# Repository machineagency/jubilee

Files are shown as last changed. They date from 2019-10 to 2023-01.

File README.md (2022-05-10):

Jubilee V2.2.2
=======

Jubilee is an open-source, extensible multi-tool motion platform capable of running GCode for non-loadbearing automation applications.

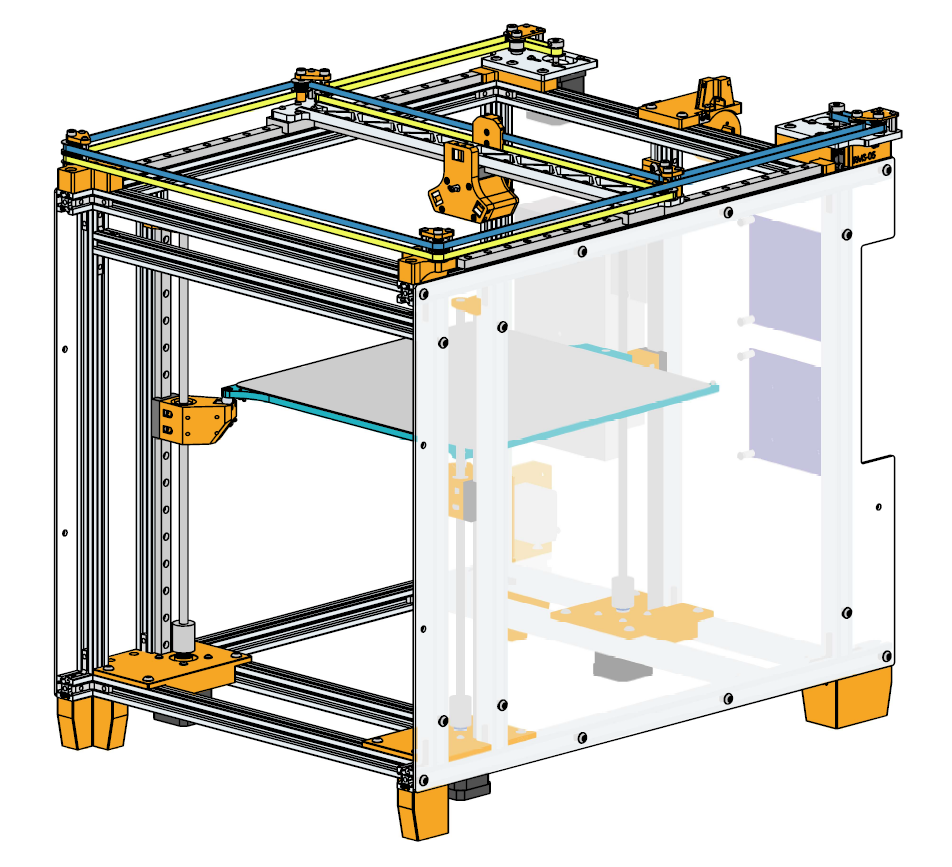
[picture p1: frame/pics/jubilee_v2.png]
Jubilee


Out-of-the-box, Jubilee is configured for multimaterial 3D printing and multicolor pen plotting, but we've had success with light liquid-handling and image stitching applications too.

While this repository contains all the design-related content needed to build a Jubilee, we suggest using the [**Wiki**](https://jubilee3d.com/index.php?title=Main_Page) to navigate through this "file soup."

## Top-Level Specs
* Automatic Toolchanging compatible with E3D tool plates
* CoreXY Motion System
* 300x300x300 build volume.
* 409mm of horizontal tool rack space
* kinematically coupled bed plate
* autotramming with 3-point bed-leveling
* ~$1350 for a single unit, not including tools. See the [BOM][bom] for the part breakdown
* User Extensible! We encourage extending the design to custom applications via custom tools and bed plates
* Full specs listed on [this wiki page](https://jubilee3d.com/index.php?title=Specs)

## Build your own Jubilee

The best way to get started is to thumb through the [**Assembly Instructions**](https://jubilee3d.com/index.php?title=Assembly_Instructions) and [**Bill of Materials**][bom] first.

Then head over to the [**Wiki**](https://jubilee3d.com/index.php?title=Main_Page) to start gathering tools and deciding which parts to buy and which parts to make.

### Downloading
There are 3 ways to work with the Jubilee source files: with and without history.
* To download the latest stable release without history, head to the [Releases](https://github.com/machineagency/jubilee/releases) page and download the latest release.
* To download the latest stable release with history and track updates, clone the project with the "Code" button above and switch to the corresponding branch.
* To download the latest stable release with history and submit additions back to the main project, create a "Fork" of the project with the button in the upper right. Then switch to the corresponding release branch in your fork of the project.

## Repository Contents
The Repository is broken into three main chunks:
* **frame** contains all design content related to the Jubilee frame
* **tools** contains all design content related to custom tools and tools to help assemble and tune Jubilee
* **software** holds both the Duet config files and profile settings for common slicer packages

inside these folders, you'll usually find a folder structure that looks like this:
* **assembly\_instructions** contains PDFs to take you step-by-step through sub-assemblies of the project.
* **cads** contains raw design files in two formats
    * **Solidworks**
    * **STEP**
* **fabrication\_exports** contains STLs, DXFs, and other files used to fabricate pieces of Jubilee

## Support

Have questions? Building your own Jubilee? **[Join the Discord!][discord]**

## Contributing

Jubilee is meant to be extended by the community. If you are interested in contributing, there are a number of ways to get involved:

* Review, comment, or add to the **[open issues](https://github.com/machineagency/jubilee/issues)**
* Have a new tool to add to the repository? Read our [contributing]() guidlelines and create a [pull request](https://help.github.com/en/github/collaborating-with-issues-and-pull-requests/creating-a-pull-request)
* **[Join the Discord!][discord]**

## Who are we?
Jubilee was designed with love by [Joshua Vasquez](http://www.doublejumpelectric.com/) of [Machine Agency](http://depts.washington.edu/machines/) at the University of Washington.

### Press and Outside Resources

Read more about the history of Jubilee on [Hackaday](https://hackaday.com/2019/11/14/jubilee-a-toolchanging-homage-to-3d-printer-hackers-everywhere/), or, for the patient, check out this (1hr) [talk](https://www.youtube.com/watch?v=7fz2UHHxe5o&t=119s) given in Jan 2020.
For more community takes, have a look at:
* [Hackster.io](https://www.hackster.io/news/jubilee-is-an-open-source-motion-platform-that-allows-for-multi-tool-fabrication-213881ee3ce1)
* 3D Distributed
    * [Best CoreXY 3D Printers 2020](https://3ddistributed.com/best-corexy-3d-printer-2020/)
    * [Best CoreXY 3D Printers 2021](https://3ddistributed.com/corexy-3d-printer/best-corexy-3d-printers-2021/)
* [All3DP](https://all3dp.com/2/3d-printer-plans-3d-printer-blueprints/)
* [3D Printing Today](https://threedprintingtoday.libsyn.com/327_3dprinting_today)

### Open Source
Jubilee is licensed under a [Creative Commons Attribution 4.0 Unported License][cc-by] (CC BY 4.0).
and [Certified Open Source Hardware](https://certification.oshwa.org/us002091.html).

[][cc-by] 

[bom]: https://docs.google.com/spreadsheets/d/1pRzBQxVzL9c4T9b1RrKvSjlSwJJhJ7NcbSV6iJUv0X0/edit#gid=0
[cc-by]: https://creativecommons.org/licenses/by/4.0/
[cc-by-image]: https://licensebuttons.net/l/by/4.0/88x31.png
[discord]: https://discord.gg/XkphRqb
[wiki]: https://jubilee3d.com/

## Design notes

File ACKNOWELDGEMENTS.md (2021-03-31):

Jubilee was built to encapsulate all the best practices in hobbyist 3D printing machine design at the time.
As a result, it's a machine that takes inspiration from many many places.
Here's the (growing!) list of referenced projects and contributors

## Design Acknowledgments
* Nadya Peek of Machine Agency
  * for the time, expenses, and infrastructure that enabled Jubilee to come together over many iterations
* Eric Moyer
  * for continuous design feedback, manufacturing insights, and help with community engagement
* Sanjay Mortimer and the E3D Team
  * for an open reference for tool coupling
* J Steve White and Tony Akens of the [Railcore](https://railcore.org/) Project
  * for an incredibly well-documented BOM, an example of 3-point bed leveling firmware configs, a great example of community engagement, and openness in sharing and answering questions
* @marioquake on Github for suggesting a well-placed spacer
* @Ocho Camino on Discord for an improved Power Inlet Socket
* @Troll on Discord for a fantastic Logo on the bed plate rendering
* @edthesped for the "Cappuccino"-tested Fan Shroud

## Manufacturing and Supplier Acknowledgements
* Matthew White at 713Maker
  * for supporting the Jubilee builder community with custom machined parts and developing the original magnetic bed plate
* Steve Wygant of SeeMeCNC
  * for supporting the Jubilee builder community with a generous variety of Jubilee's laser-cut and machined parts.
* Wade Wendorf at Mandala Rose Works
  * for supporting the Jubilee builder community with custom machined upgrade parts of various types
* Luke at Luke's Laboratory
  * for kit-izing various elements of the project, making them cheaper for Jubilee builders
* Rebecca and Jason of LDO Motors
  * for supplying custom motor options for the toolchanger elastic lock design

## Grants and Donations
Jubilee is made possible through monetary support and donations from
* the 2019 [Tool Foundry](https://www.toolfoundry.org/) Boot Camp Accelerator
* The E3D Team
* Tony Lock of the Duet3D Project

## Beta Testing and Design Feedback Acknowledgements
* Andrew Waer for an early V1 build with assembly feedback and research into trade-offs regarding various documentation styles
* Cindy Feng for an early V2 build with extensive feedback
* Kellie Dunn for an early V2 build with extensive feedback
* @Danal on Discord for early design feedback and identifying early stage bugs

## BOM and Documentation Acknoweldgements
* @ImpC on Discord for BOM alternatives to cut costs
* @VinnyCordeiro on Discord for contributing a massive list of laser cutting services to the wiki
* @MiasmicTruth on Discord for live assembly videos and continuous assembly instruction feedback
* @Bryan H. on Discord for part numbering scheme suggestions and printed part fabrication suggestions
* @Enza3D on Discord for part numbering scheme suggestions
* @RexOrient on Discord for Duet3 Wiring Diagrams

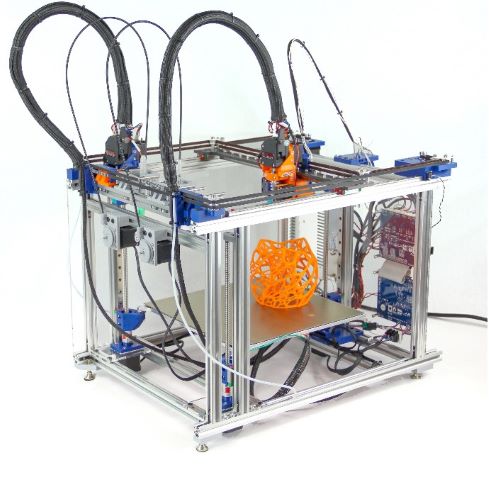
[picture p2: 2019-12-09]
frame/pics/jubilee-professional-headshot-brightened.jpg

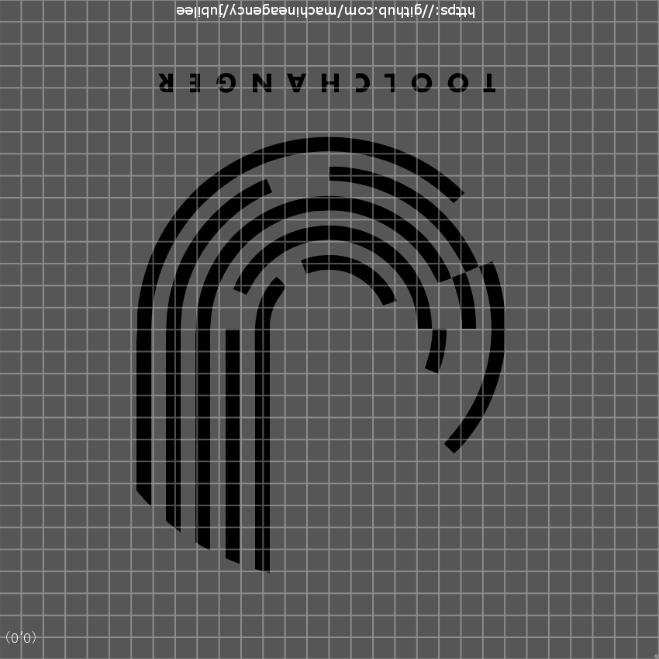
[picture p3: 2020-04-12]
software/slicer_settings/prusa_slic3r/bed_rendering/Jubilee_Bed_Graphic.png

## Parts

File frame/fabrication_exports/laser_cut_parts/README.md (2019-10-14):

## Notes on File Types

Most laser cutters will directly trace the lines and arcs present in a DXF file. For these laser cutters, use the **offset** files.

For the few laser cutters that perform *kerf compensation*, use the **original** files.

If you are unsure, using the **offset** files is probably your best bet.

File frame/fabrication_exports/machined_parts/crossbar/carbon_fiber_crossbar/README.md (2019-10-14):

## Getting a Crossbar

To have this part made for you, send this DXF to cncmadness@gmail.com. Request that this part be made out of **6mm carbon fiber plain-weave**. The estimated price for this part is between $50 and $60.

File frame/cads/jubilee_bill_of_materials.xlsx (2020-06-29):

ITEM NO. | QTY. | DESCRIPTION | Part Num | Part Num Short | Stock Material | Fab Process | Vendor | Vendor Num
1 | 1 | Twist Lock Shaft |  |  | Stainless Steel | Machined
2 | 7 | 409mm TSlot Extrusion |  |  |  |  | Misumi | HFS5-2020-409
3 | 4 | 604mm long TSlot Extrusion |  |  |  |  | Misumi | HFS5-2020-604
4 | 7 | 430mm 2020 TSlot Extrusion |  |  |  |  | Misumi | HFS5-2020-430
5 | 4 | MGN12C Carriage Block |  |  |  |  | Aliexpress | n/a
6 | 2 | MGN12H Carriage Block |  |  |  |  | Aliexpress | n/a
7 | 3 | length@mgn12_rail_400mm.SLDPRTmm long MGN12 rail |  |  |  |  | Aliexpress
8 | 1 | length@mgn12_rail_395mm.SLDPRTmm long MGN12 rail |  |  |  |  | Aliexpress | n/a
9 | 2 | 450"mm long $PRP:"SW-Configuration Name |  |  |  |  | Aliexpress
10 | 6 | 20T Idler pulley, 2GT, 5mm bore |  |  |  |  | Amazon | B07GLQMMLJ
11 | 2 | 20T toothless idler, 5mm bore |  |  |  |  | Amazon | B071KK6Z8X
12 | 1 | Duet Ethernet Expansion Board |  |  |  |  | Duet3d
13 | 1 | Duet Ethernet |  |  |  |  | Duet3d
14 | 3 | 8mm T8x2 Trapezoidal Lead Screw |  |  |  |  | ZYLTech | HW-SC-T8x2-Delrin-CUTSMALL
15 | 3 | 5mm to 8mm flexible plumb coupler |  |  |  |  | ZYLtech | HW-CP-PUM-5x8
16 | 3 | 8mm T8x2 Small Delrin Anti-Backlash Nut |  |  |  |  | ZYLTech | n/a
17 | 2 | 16-T 2GT Drive Pulley for 6mm belt |  |  |  |  | E3D-Online | M-PULLEY-GT2-16T-6-P5-C-H155
18 | 2 | 20T Idler pulley, 2GT, 5mm bore |  |  |  |  | Amazon | B07GLQMMLJ
19 | 2 | 20T Toothless Idler pulley, 2GT, 5mm bore
20 | 1 | Upper Belt
21 | 1 | Lower Belt
22 | 1 | Hub, 6mm bore |  |  |  |  | Filastruder
23 | 27 | M3 Slide In T Nuts
24 | 3 | 10mm steel balls with M4 threads |  |  |  |  | Newegg | DZ6YTSFkoC
25 | 1 | Bed Plate |  |  | 6.35mm MIC6 Aluminum | Machined | 713Maker
26 | 1 | Pocketed Crossbar |  |  | 6mm carbon fiber plain weave |  | Mandala Rose Works
27 | 1 | Machined Left Motor Corner Bracket | 021-LMP-02-M61 | LMP-02 | 6061 | Machined | Mandala Rose Works
28 | 1 | Machined Right Motor Corner Bracket | 021-RMP-02-M61 | RMP-02 | 6061 | Machined | Mandala Rose Works
29 | 1 | M3 Square Nut |  |  |  |  | Misumi | HNSQ3-3
30 | 1 | 24V Power Supply |  |  |  |  | Amazon | B01IOK5FM0
31 | 1 | IEC320 C14 120V Power Socket |  |  |  |  | Amazon | B07C184P7L
32 | 56 | Interior Inside Corner Bracket |  |  |  |  | Amazon | B07F2K8SN7
33 | 89 | M5 Drop-In T-Nut for 20x20 Extrusion |  |  |  |  | Amazon | B01FOC6A8E
34 | 4 | OpenBuilds M5 3mm Spacer
35 | 5 | Nema 17 Stepper Motor |  |  |  |  | Stepper Online | 17HM19-2004S or 17HM19-2004S1
36 | 1 | Nema 11 Planetary Stepper,13.76:1, 1A |  |  |  |  | Stepper Online | 14HS13-0804S-PG5
37 | 16 | M5 Shim, 0.2mm thick, 7mm OD |  |  |  |  | Misumi | CIMRS5-7-0.2
38 | 1 | M3 Set Screw, 5mm long |  |  |  |  | McMaster-Carr | 92029A102
39 | 3 | M2 Screw, 10mm long |  |  |  |  | McMaster-Carr | 91292A833
40 | 19 | M3 Buttonhead Screw, 6mm long |  |  |  |  | McMaster-Carr | 92095A179
41 | 72 | M3 Buttonhead Screw, 8mm long |  |  |  |  | McMaster-Carr | 92095A181
42 | 53 | M3 Buttonhead Screw, 10mm long |  |  |  |  | McMaster-Carr | 92095A182
43 | 12 | M3 Buttonhead Screw, 12mm long |  |  |  |  | McMaster-Carr | 92095A183
44 | 1 | M3 Buttonhead Screw, 16mm long |  |  |  |  | McMaster-Carr | 92095A184
45 | 1 | M3 Buttonhead Screw, 20mm long |  |  |  |  | McMaster-Carr | 92095A185
46 | 4 | M4 Buttonhead Screw, 6mm long |  |  |  |  | McMaster-Carr | 92095A188
47 | 16 | M4 Buttonhead Screw, 8mm long |  |  |  |  | McMaster-Carr | 92095A189
48 | 2 | M4 Buttonhead Screw, 10mm long |  |  |  |  | McMaster-Carr | 92095A190
49 | 46 | M5 Buttonhead Screw, 8mm long |  |  |  |  | McMaster-Carr | 92095A207
50 | 27 | M5 Buttonhead Screw, 10mm long |  |  |  |  | McMaster-Carr | 92095A208
51 | 10 | M5 Buttonhead Screw, 20mm long |  |  |  |  | McMaster-Carr | 92095A214
52 | 4 | M5 Buttonhead Screw, 30mm long |  |  |  |  | McMaster-Carr | 92095A218
53 | 2 | M3 Flathead Screw, 10mm long |  |  |  |  | McMaster-Carr | 92125A130
54 | 3 | M4 Flathead screw, 10mm long |  |  |  |  | McMaster-Carr | 92125A190
55 | 1 | M3 Set Screw, 3mm long |  |  |  |  | McMaster-Carr | 92015A101
56 | 1 | M3 Set Screw, 8mm long |  |  |  |  | McMaster-Carr | 91390A101
57 | 2 | M4 Set Screw, 25mm long |  |  |  |  | McMaster-Carr | 92605A124
58 | 16 | M3 Locknut |  |  |  |  | McMaster-Carr | 93625A100
59 | 2 | M4 Locking Nut |  |  |  |  | McMaster-Carr | 93625A150
60 | 22 | M3 Washer |  |  |  |  | McMaster-Carr | 90965A130
61 | 8 | M4 Nylon Washer |  |  |  |  | McMaster-Carr | 95610A150
62 | 1 | M3 Dowel Pin, 12mm long |  |  |  |  | McMaster-Carr | 91585A371
63 | 12 | M4 Dowel Pin, 20mm long |  |  |  |  | McMaster-Carr | 91585A457
64 | 4 | M4 Shoulder Screw, 16mm-l, 5mm-d |  |  |  |  | McMaster-Carr | 90265A132
65 | 6 | M4 Shoulder Screw, 25mm long |  |  |  |  | McMaster-Carr | 90278A375
66 | 1 | M3 10mm standoff, 4.5mm wide |  |  |  |  | McMaster-Carr | 95947A006
67 | 4 | M3 Standoff, 14mm long, 6mm wide |  |  |  |  | McMaster-Carr | 95947A045
68 | 5 | M3 Standoff, 20mm long, 6mm wide |  |  |  |  | McMaster-Carr | 95947A054
69 | 8 | M4 Standoff, 12mm long |  |  |  |  | McMaster-Carr | 95947A041
70 | 22 | M3 Tapered Heat Set Insert |  |  |  |  | McMaster-Carr | 94180A331
71 | 4 | M4 Tapered Long Heat Set Insert |  |  |  |  | McMaster-Carr | 94180A353
72 | 4 | M5 Washer, 0.8-1.2mm thick |  |  |  |  | McMaster-Carr | 98687A110
73 | 3 | M5 Shim, 0.2mm thick, 10mm OD |  |  |  |  | McMaster-Carr | 98089A246
74 | 1 | M6 Shim, 0.2mm thick |  |  |  |  | McMaster-Carr | 98089A247
75 | 1 | E-Clip |  |  |  |  | McMaster-Carr | 98543A103
76 | 1 | Sleeve Bearing, 6mm bore, 10mm long |  |  |  |  | McMaster-Carr | 6658K726
77 | 2 | M5 Buttonhead Screw, 14mm long |  |  |  |  | McMaster-Carr | 92095A211
78 | 3 | 5mm Oversize Thrust Bearing |  |  |  |  | McMaster-Carr | 6655K51
79 | 1 | Ring Lug Thermistor |  |  |  |  | Digikey | BC2891-ND
80 | 2 | Mechanical Limit Switch |  |  |  |  | Digikey | SS0750300F070P1A-ND
81 | 1 | 3-32V Solid State Relay |  |  |  |  | Digikey | CC1006-ND
82 | 3 | Dust-Proof Limit Switch |  |  |  |  | Digikey | SW1153-ND
83 | 3 | Bent Solder Terminal Lug |  |  |  |  | Digikey | 36-4000-ND
84 | 2 | Bent M3 Solder Terminal Lug (Bend A) |  |  |  |  | Digikey | 36-7328-ND
85 | 3 | Bent M3 Solder Terminal Lug (Bend A) |  |  |  |  | Digikey | 36-4000-ND
86 | 1 | Front Left Z Motor Plate | 10-LZP-03-PPL | LZP-03 | PLA | Printed
87 | 1 | Front Right Z Motor Plate | 10-LZP-03-PPL | LZP-03 | PLA | Printed
88 | 1 | Back Z Motor Plate | 10-BZP-03-PPL | BZP-03 | PLA | Printed
89 | 1 | Back Right Foot | 10-BRF-05-PPL | BRF-05 | PLA | Printed
90 | 1 | Back Left Foot | 10-BRF-05-PPL | BRF-05 | PLA | Printed
91 | 1 | Front Right Foot | 10-BRF-05-PPL | BRF-05 | PLA | Printed
92 | 1 | Front Left Foot | 10-BRF-05-PPL | BRF-05 | PLA | Printed
93 | 3 | Z Thrust Bearing Spacer |  |  | PLA | Printed
94 | 1 | Left Corner Pulley Plate | 03-LCP-02-PPL | LCP-02 | PLA | Printed
95 | 1 | Left Corner Pulley Plate | 03-RCP-02-PPL | RCP-02 | PLA | Printed
96 | 1 | Right Motor Spacer | 02-RMS-05-PPE | RMS-05 | PLA | Printed
97 | 1 | Lock Actuator Base Plate | 05-RLB-10-PPL | RLB-10 | PLA | Printed
98 | 1 | Left Motor Spacer | 02-LMS-04-PPE | LMS-04 | PLA | Printed
99 | 2 | Belt Clasp | 06-BCL-02-PPL | BCL-02 | PLA | Printed
100 | 1 | Carriage Center Plate | 06-CCP-04-PPL | CCP-04 | PLA | Printed
101 | 1 | Carriage Back Plate | 06-CCP-04-PPL | CCP-04 | PLA | Printed
102 | 1 | Carriage Front Plate | 06-CCP-04-PPL | CCP-04 | PLA | Printed
103 | 1 | Spring Guide Capture | 06-CCP-04-PPL | CCP-04 | PLA | Printed
104 | 1 | Carriage Pulley | 06-CPL-01-PPL | CPL-01 | PLA | Printed
105 | 1 | Back Leadscrew Retainer | 12-BLR-03-PPL | BLR-03 | PLA | Printed
106 | 1 | Front Left Leadscrew Retainer | 12-LLR-03-PPL | LLR-03 | PLA | Printed
107 | 1 | Front Right Leadscrew Retainer | 12-LLR-03-PPL | LLR-03 | PLA | Printed
108 | 3 | Printed Pulley Spacer |  |  | PLA | Printed
109 | 1 | Left Bed Coupler | 12-RBC-04-PPL | RBC-04 | PLA | Printed
110 | 1 | Right Bed Coupler | 12-RBC-04-PPL | RBC-04 | PLA | Printed
111 | 1 | Back Bed Coupler | 12-BBC-04-PPL | BBC-04 | PLA | Printed
112 | 2 | pulley reinforcement plate for motor | -MRP-01- | MRP-01 | PLA | Printed
113 | 1 | Left Crossbar Pulley Reinforcement Plate | 041-LXR-03-PPL | LXR-03 | PLA | Printed
114 | 1 | Right Crossbar Pulley Reinforcement Plate | 041-RXR-03-PPL | RXR-03 | PLA | Printed
115 | 1 | PSU Socket Holder | 09-PSH-02-PPL | PSH-02 | PLA | Printed
116 | 1 | Spring Guide Anchor Block | 05-RLB-10-PPL | RLB-10 | PLA | Printed
117 | 1 | Lock Actuator Motor Clip |  |  | PLA | Printed
118 | 1 | REL Knob |  |  | PLA | Printed
119 | 1 | Fixed Pulley |  |  | PLA | Printed
120 | 1 | Left Corner Pulley Reinforcement Plate | 03-LCR-03-PPL | LCR-03 | PLA | Printed
121 | 1 | Left Corner Pulley Reinforcement Plate | 03-LCR-03-PPL | LCR-03 | PLA | Printed
122 | 1 | Crossbar X Limit Trigger |  |  | PLA | Printed
123 | 1 | Floating Pulley |  |  | PLA | Printed
124 | 1 | Twist Lock Spacer |  |  | PLA | Printed
125 | 1 | Left Side Panel |  |  | 3mm Acrylic Sheet | Laser Cut
126 | 1 | Right Side Panel |  |  | 3mm Acrylic Sheet | Laser Cut
127 | 1 | Back Panel |  |  | 3mm Acrylic Sheet | Laser Cut
128 | 1 | Magnetic Sheet (305x305mm) |  |  |  |  | Subtle.Design

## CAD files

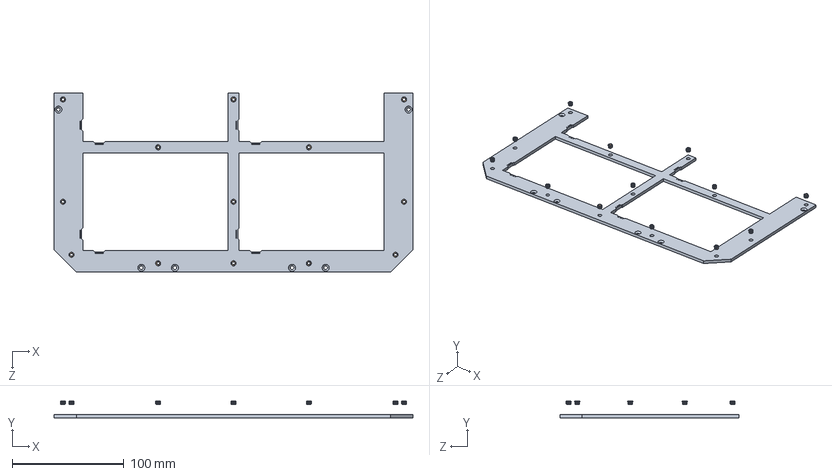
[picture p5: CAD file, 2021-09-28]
bed_plates/6x_well_plate_bed/cads/Solidworks/top_layer_bottom_plate_with_inserts.SLDASM
321.0 x 15.1 x 160.5 mm
segmented_6_slot_bed_attachment
m3_heat_set_insert_tokai_ud-43030 x 13

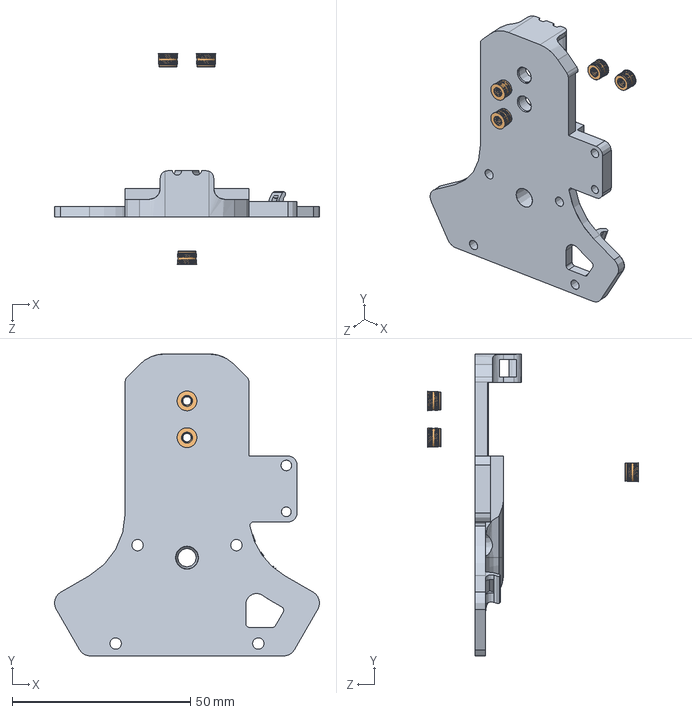
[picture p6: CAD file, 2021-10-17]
frame/cads/Solidworks/jubilee_frame/carriage/carriage_back_plate_with_inserts.SLDASM
74.3 x 84.7 x 59.2 mm
carriage
m3_heat_set_insert_94180A331 x 4

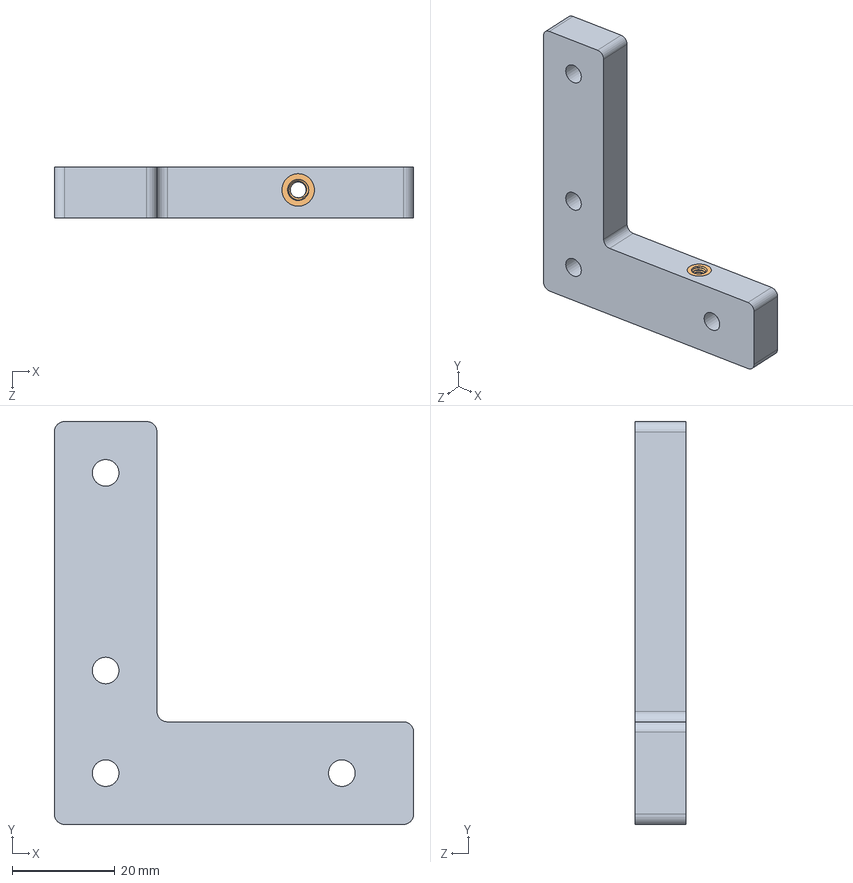
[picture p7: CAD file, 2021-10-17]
frame/cads/Solidworks/jubilee_frame/motion_stage/assemblies/short_motor_corner_plate_spacer_with_insert.SLDASM
70.0 x 78.5 x 10.0 mm
motor_corner_bracket_spacer
m4_heat_set_insert_long_94180A353

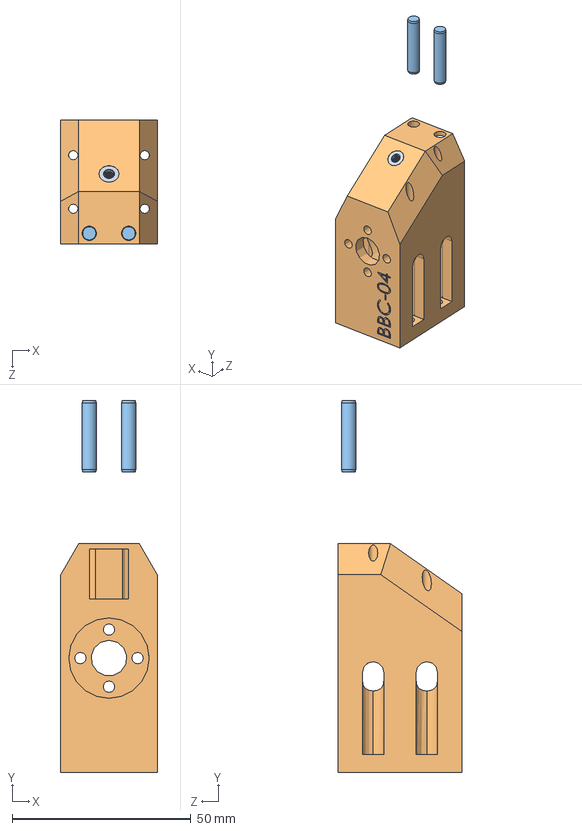
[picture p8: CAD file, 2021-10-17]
frame/cads/Solidworks/jubilee_frame/motion_stage/z_axis/kinematic_coupling/back_coupling_plate_with_inserts.SLDASM
27.0 x 104.1 x 34.7 mm
m3_heat_set_insert_94180A331
bed_coupling_back_plate
dowel_pin_4mm_d_20mm_l_91585A457 x 2

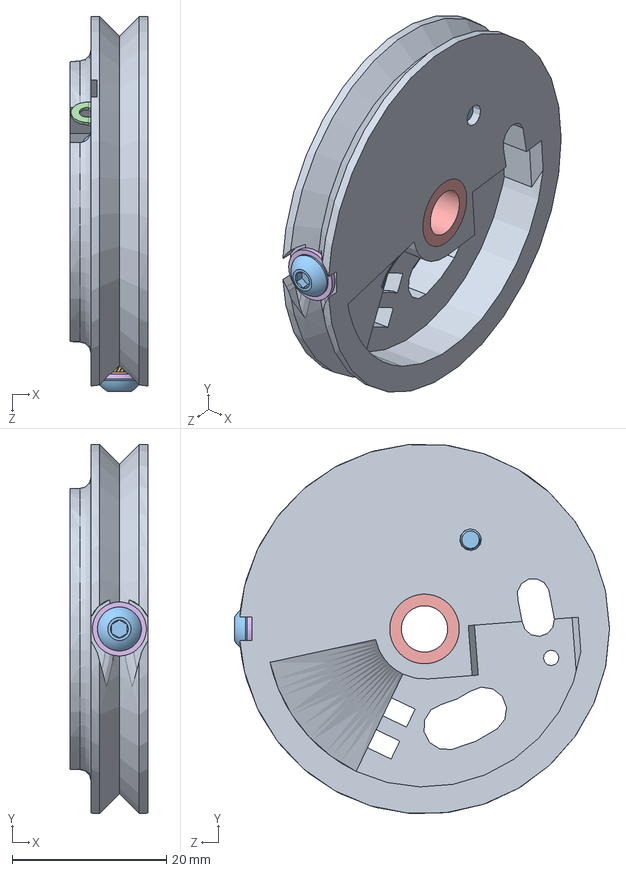
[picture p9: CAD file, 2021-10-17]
frame/cads/Solidworks/jubilee_frame/remote_elastic_lock/floating_half_pulley_assembly.SLDASM
10.1 x 47.9 x 48.7 mm
rel_half_pulley
m3_heat_set_insert_94180A331
m3_6mm_buttonhead_screw_92095A179 x 2
7328_solder_terminal_lug
6mm_sleeve_bearing_10mm_long_6658K726
m3_stainless_steel_washer_90965A130

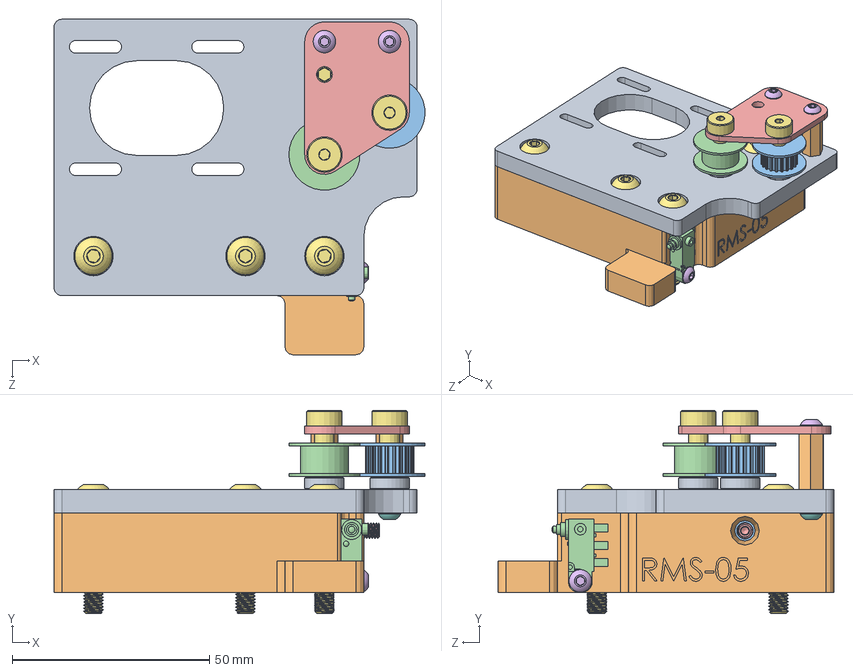
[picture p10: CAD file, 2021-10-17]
frame/cads/Solidworks/jubilee_frame/upgrades/alum_motor_bracket/machined_right_motor_plate_assembly.SLDASM
94.0 x 51.5 x 85.0 mm
alum_motor_corner_bracket
m3_14mm_hex_standoff_6mm_wide_95947A045 x 2
20t_idler_5mm_bore
20t_toothless_idler_5mm_bore
motor_plate_reinforcement
m3_6mm_buttonhead_screw_92095A179 x 2
m4_shoulder_screw_5mm_d_16mm_l_90265A132 x 2
m5_shim_0.2mm_thick_PCIMRS5-7-0.2 x 2
openbuilds_spacer_3mm_tall_10mm_od x 2
motor_corner_bracket_spacer
m4_heat_set_insert_long_94180A353
D2HW_C201H
m4_set_screw_25mm_92605A124
m3_8mm_buttonhead_screw_92095A181
m5_30mm_buttonhead_screw_92095A218 x 4
m3_10mm_buttonhead_screw_92095A182 x 2

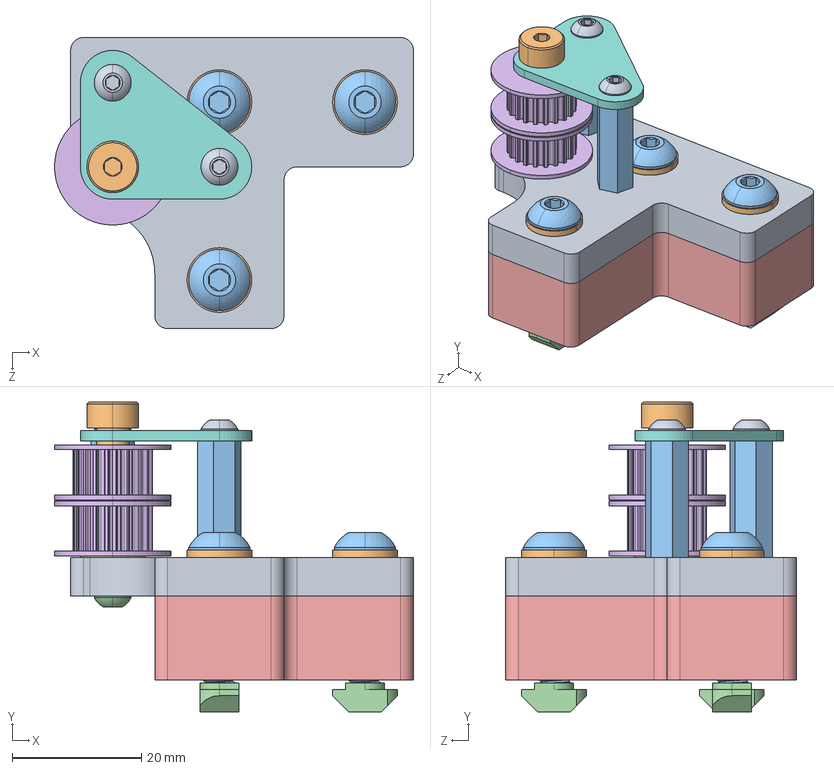
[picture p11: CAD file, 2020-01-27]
frame/upgrades/aluminum_corner_plates/cads/STEP/left_double_pulley_corner_bracket_assembly.STEP
55.5 x 47.9 x 45.0 mm
alum_double_pulley_corner_bracketr_Left Double Pulley Corner Bracket
m4_shoulder_screw_5mm_d_20mm_l_90278A374_90278A374
m3_18mm_hex_standoff_6mm_wide_95947A525_95947A525 x 2
m3_10mm_buttonhead_screw_92095A182_92095A182 x 2
double_pulley_corner_bracket_Left Machined Bracket Spacer
20t_idler_5mm_bore x 2
m5_shim_0.2mm_thick_98089A246_98089A246 x 2
back_pulley_reinforcement_plate
m3_6mm_buttonhead_screw_92095A179_92095A179 x 2
m5_stainless_steel_washer_90965A160_90965A160 x 3
m5_25mm_buttonhead_screw_92095A216_92095A216 x 3
m5_locking_t_nut_20x20_generic x 3

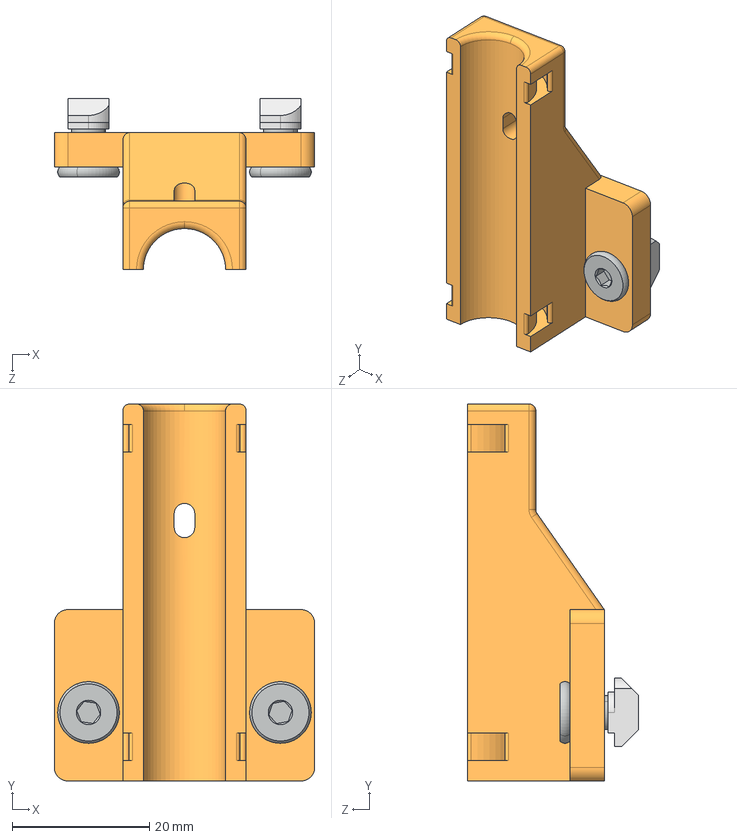
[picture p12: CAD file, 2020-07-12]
tools/jubilee_tools/tools/base_tool/cads/tool_cable_management_bracket/STEP/tool_cable_management_assembly.STEP
38.0 x 55.0 x 25.0 mm
tool_cable_management_bracket
m5_low_profile_screw_template_M5 x 10 x 2
m5_locking_t_nut_20x20_generic x 2

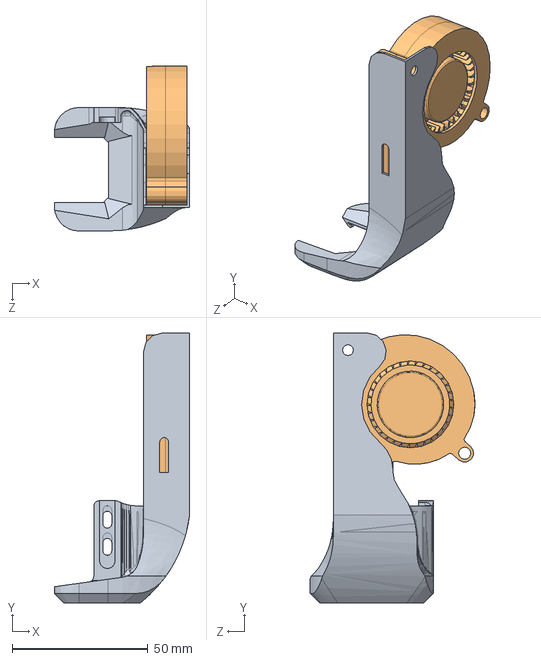
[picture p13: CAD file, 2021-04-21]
tools/jubilee_tools/tools/extruders/direct_drive_bondtech_groovemount_extruder/cads/Solidworks/fan_with_shroud_5015.SLDASM
49.8 x 99.5 x 60.8 mm
COOLING-NOZZLE-edthesped
Radial-Cooling-Fan-5015-DC12V

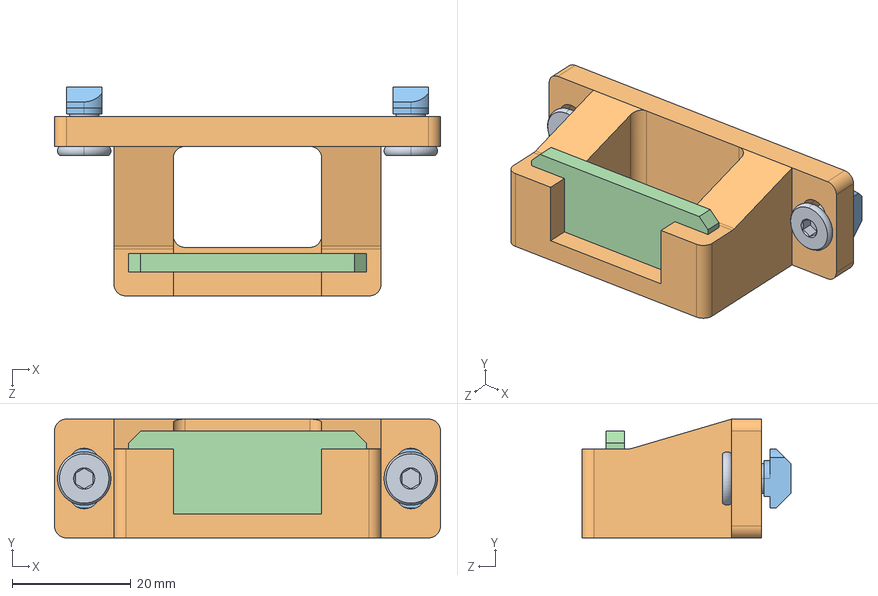
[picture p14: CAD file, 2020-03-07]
tools/jubilee_tools/tools/extruders/direct_drive_bondtech_groovemount_extruder/cads/STEP/ooze_wiper_assembly.STEP
65.0 x 20.0 x 35.2 mm
m5_low_profile_screw_template_M5 x 10 x 2
ooze_wiper_v1
m5_locking_t_nut_20x20_generic x 2
silicone_wiper

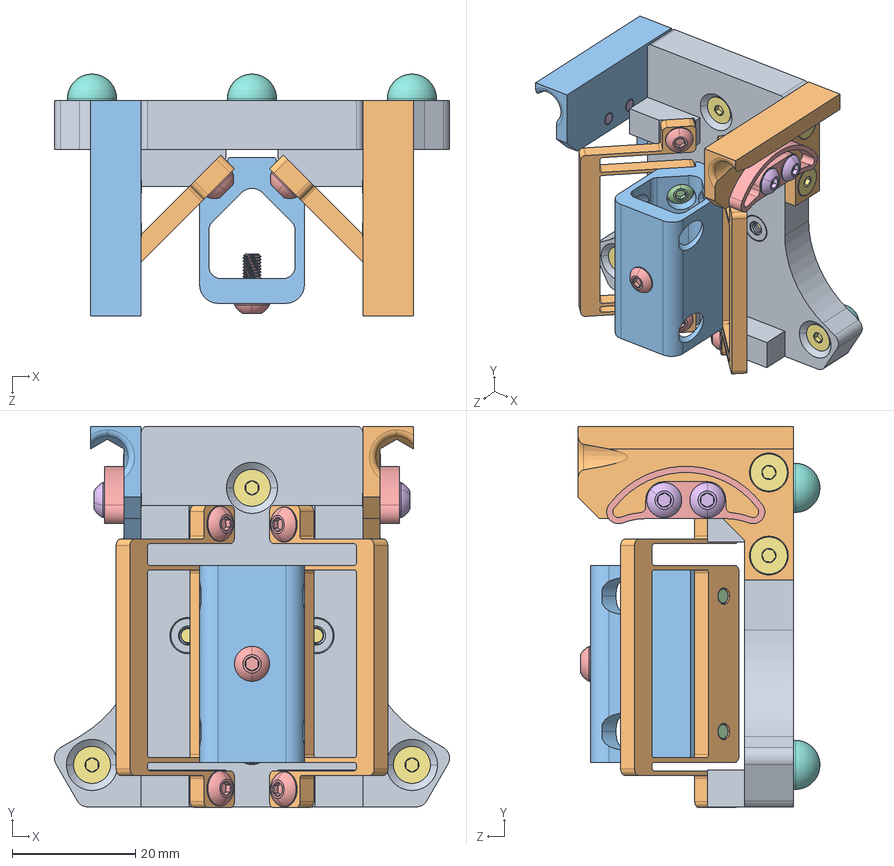
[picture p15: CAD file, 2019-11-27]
tools/jubilee_tools/tools/passive_pen_tool/cads/STEP/passive_pen_tool_assembly.STEP
64.2 x 62.0 x 39.3 mm
pen_tool_base_tool_plate_tool plate
pen_tool_base_tool_plate_right parking wing
pen_tool_base_tool_plate_left parking wing
pen_tool_base_tool_plate_v-groove locking plate
pen_tool_base_tool_plate_compression flexure x 2
m3_6mm_buttonhead_screw_92095A179_92095A179 x 4
m3_6mm_flathead_screw_92125A126_92125A126 x 10
m3_threaded_ball x 3
m3_heat_set_insert_94180A331_94180A331 x 4
pen_tool_flexure x 2
pen_holder
m3_4mm_buttonhead_screw_92095A471_92095A471 x 4
m3_8mm_buttonhead_screw_92095A181_92095A181 x 5

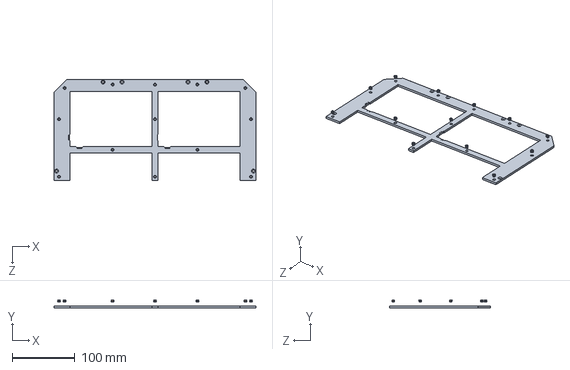
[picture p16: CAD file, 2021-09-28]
bed_plates/6x_well_plate_bed/cads/Solidworks/bottom_layer_upper_plate_with_inserts.SLDASM
321.0 x 12.0 x 160.5 mm
segmented_6_slot_bed_attachment
m3_heat_set_insert_tokai_ud-43030 x 13

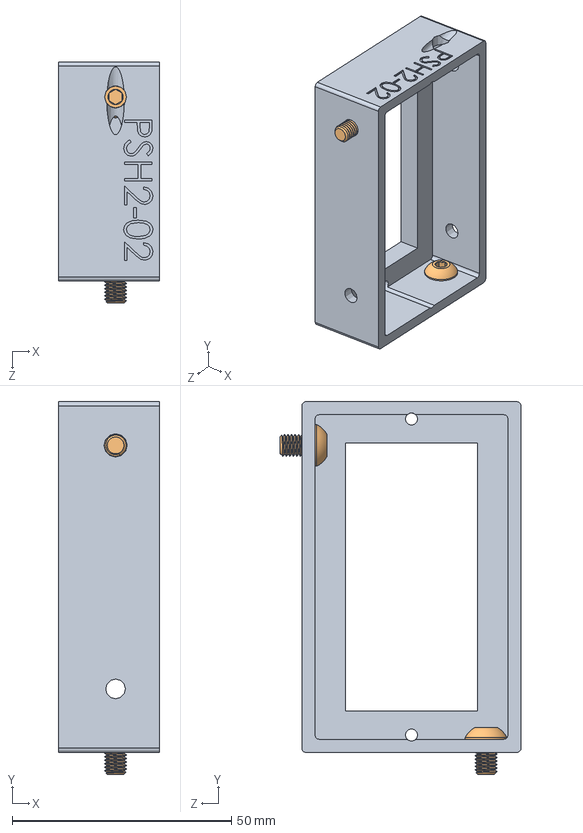
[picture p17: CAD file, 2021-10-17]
frame/cads/Solidworks/jubilee_frame/electronics/psu_socket_assembly.SLDASM
23.0 x 85.0 x 55.0 mm
psu_socket_holder
m5_8mm_buttonhead_screw_92095A207 x 2

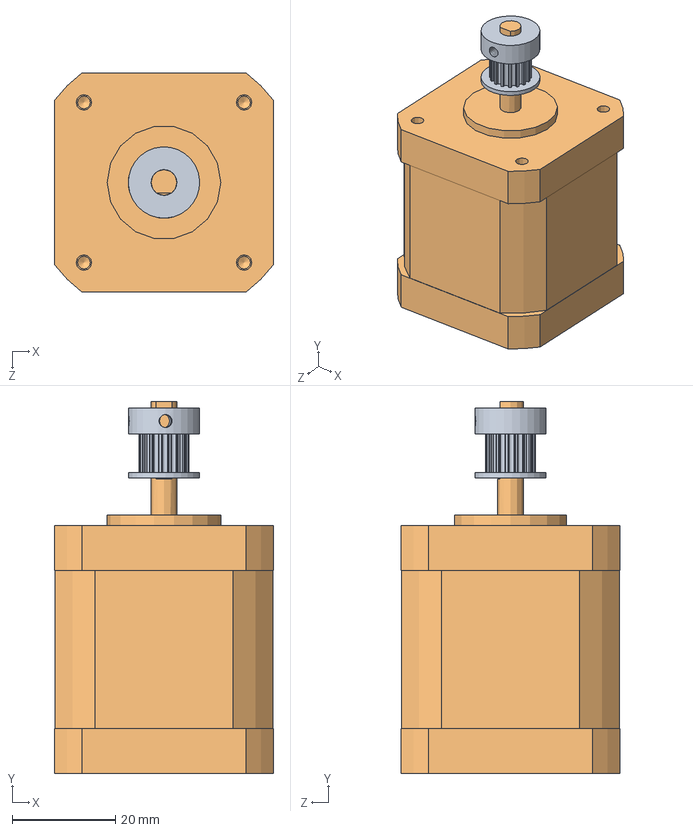
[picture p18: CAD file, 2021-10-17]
frame/cads/Solidworks/jubilee_frame/motion_stage/assemblies/xy_drive_stepper.SLDASM
42.4 x 72.0 x 42.4 mm
drive_pulley_16t_gt2_6mm_belt
17HM19-2004S

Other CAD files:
frame/cads/Solidworks/jubilee_frame/remote_elastic_lock/rel_base_with_inserts.SLDASM
frame/cads/Solidworks/jubilee_frame/upgrades/alum_motor_bracket/machined_left_motor_plate_assembly.SLDASM
frame/upgrades/aluminum_corner_plates/cads/STEP/right_double_pulley_corner_bracket_assembly.STEP
tools/jubilee_tools/tool_posts/configurable_tool_post/cads/Solidworks/tool_holder_assembly.SLDASM
bed_plates/6x_well_plate_bed/cads/Solidworks/5205_keystone.SLDPRT
bed_plates/6x_well_plate_bed/cads/Solidworks/96 Well Plate, F-bottom, Standard.SLDPRT
bed_plates/6x_well_plate_bed/cads/Solidworks/base_plate_sandwich_assembly.SLDASM
bed_plates/6x_well_plate_bed/cads/Solidworks/bed_plate_assembly.SLDASM
bed_plates/6x_well_plate_bed/cads/Solidworks/m3_16mm_flathead_screw_92125A134.SLDPRT
bed_plates/6x_well_plate_bed/cads/Solidworks/m3_8mm_flathead_screw_92125A128.SLDPRT
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

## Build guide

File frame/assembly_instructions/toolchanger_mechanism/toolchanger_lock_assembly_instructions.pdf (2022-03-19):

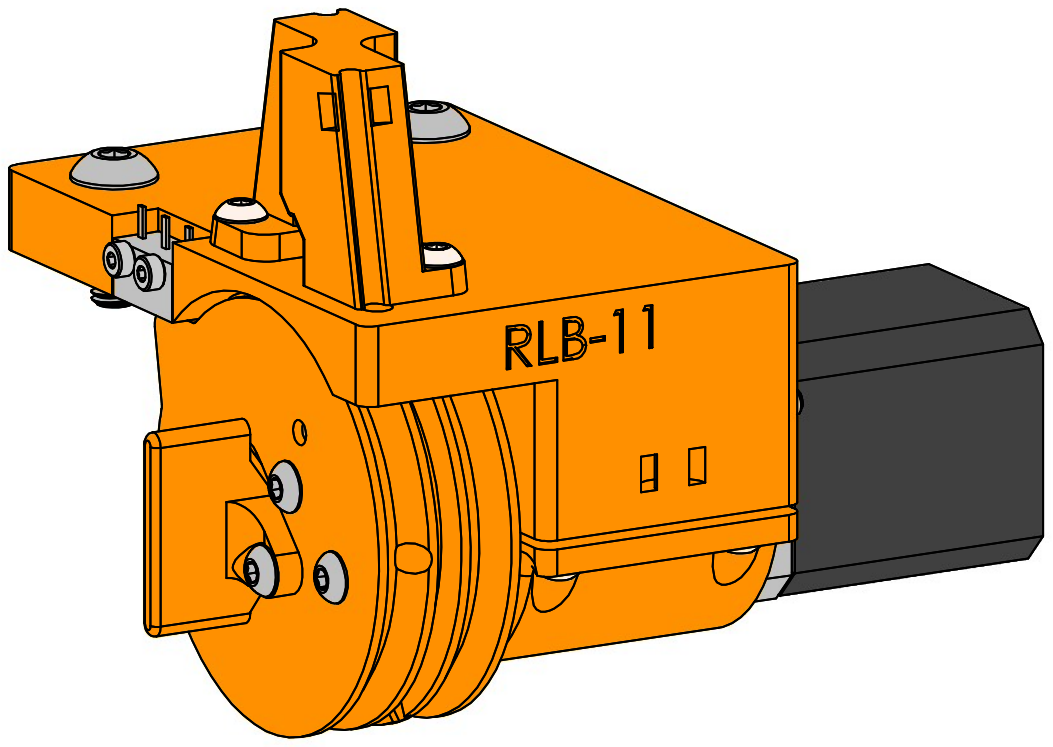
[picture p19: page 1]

Remote Elastic Lock Assembly

Created by: Created by: Joshua Vasquez Joshua Vasquez | last edited: 3/19/2022 3/19/2022

SCALE: 1:1 | SHEET 1 OF 17

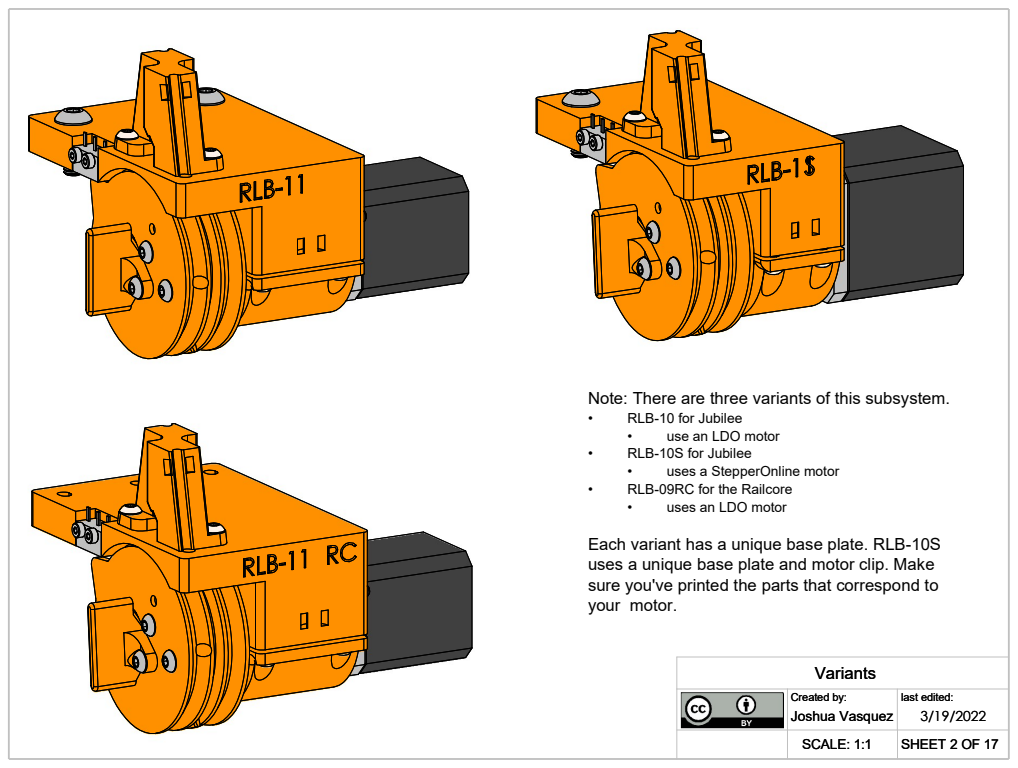
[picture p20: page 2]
Variants

Note: There are three variants of this subsystem.
• RLB-10 for Jubilee
• use an LDO motor
• RLB-10S for Jubilee
• uses a StepperOnline motor
• RLB-09RC for the Railcore
• uses an LDO motor
Each variant has a unique base plate. RLB-10S
uses a unique base plate and motor clip. Make
sure you've printed the parts that correspond to
your motor.

Created by: Created by: Joshua Vasquez Joshua Vasquez | last edited: 3/19/2022 3/19/2022

SCALE: 1:1 | SHEET 2 OF 17

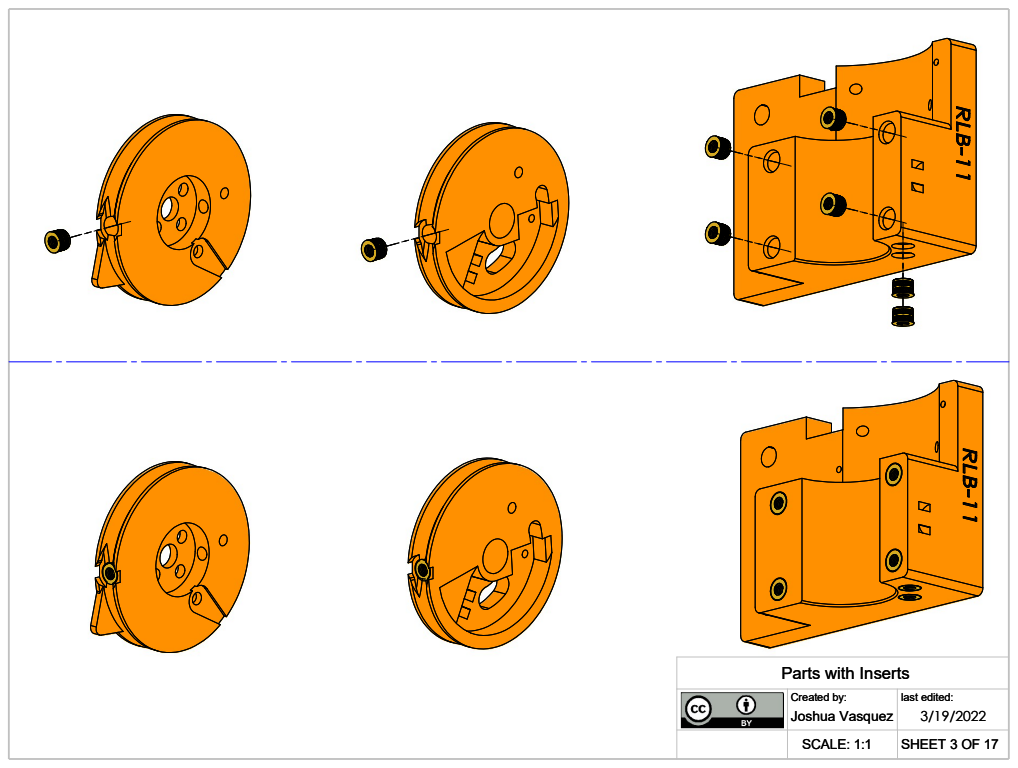
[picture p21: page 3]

Parts with Inserts

Created by: Created by: Joshua Vasquez Joshua Vasquez | last edited: last edited: 3/19/2022 3/19/2022

SCALE: 1:1 | SHEET 3 OF 17

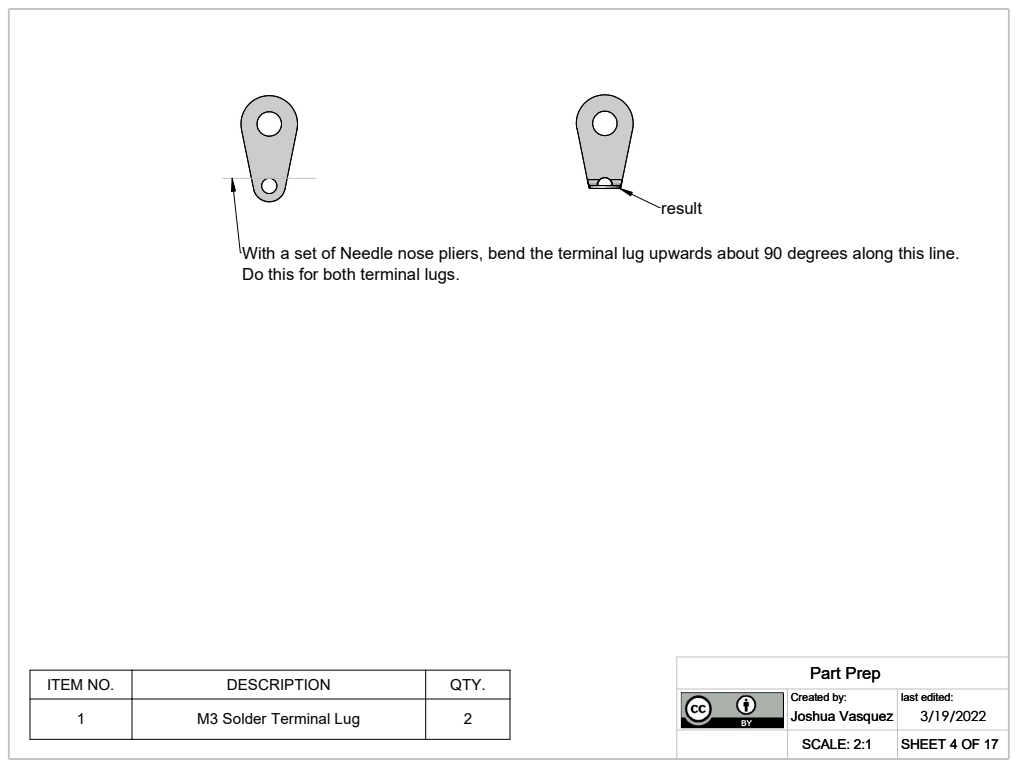
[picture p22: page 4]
Part Prep; result

With a set of Needle nose pliers, bend the terminal lug upwards about 90 degrees along this line.
Do this for both terminal lugs.

ITEM NO. | DESCRIPTION | QTY.

Created by: Created by: Joshua Vasquez Joshua Vasquez | last edited: last edited: 3/19/2022

1 | M3 Solder Terminal Lug | 2

SCALE: 2:1 | SHEET 4 OF 17

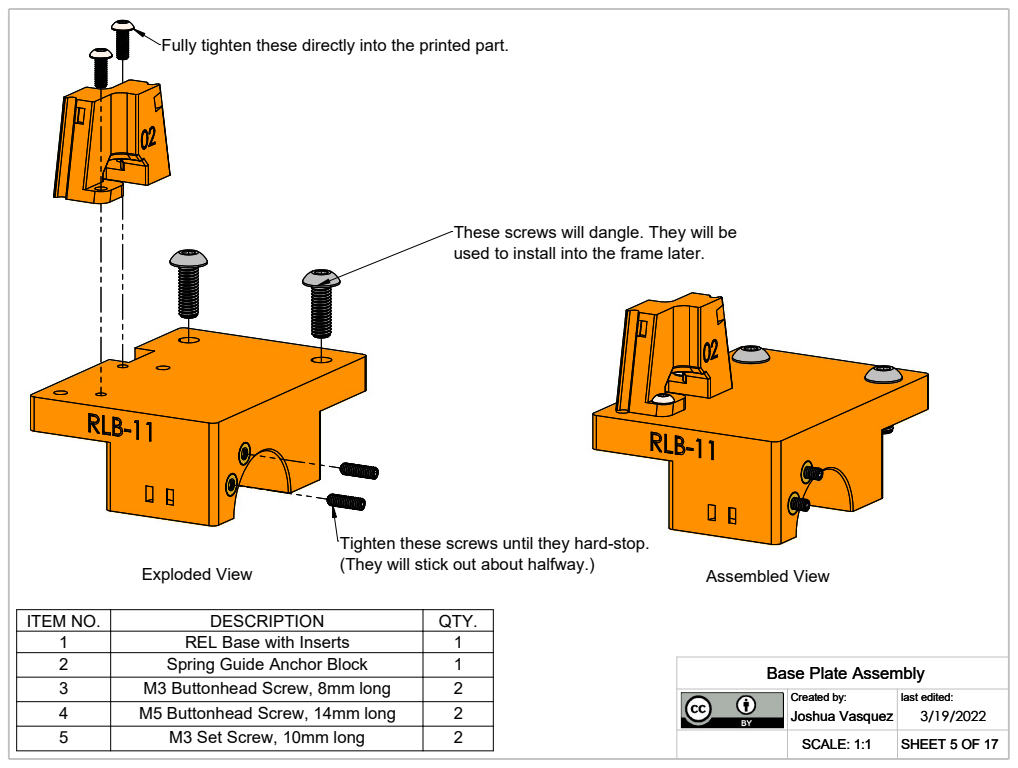
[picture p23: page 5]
Exploded View; Assembled View

Fully tighten these directly into the printed part.

These screws will dangle. They will be
used to install into the frame later.

Tighten these screws until they hard-stop.
(They will stick out about halfway.)

ITEM NO. | DESCRIPTION | QTY.
1 | REL Base with Inserts | 1
2 | Spring Guide Anchor Block | 1
3 | M3 Buttonhead Screw, 8mm long | 2
4 | M5 Buttonhead Screw, 14mm long | 2
5 | M3 Set Screw, 10mm long | 2

Base Plate Assembly

Created by: Created by: Joshua Vasquez Joshua Vasquez | last edited: last edited: 3/19/2022 3/19/2022

SCALE: 1:1 | SHEET 5 OF 17

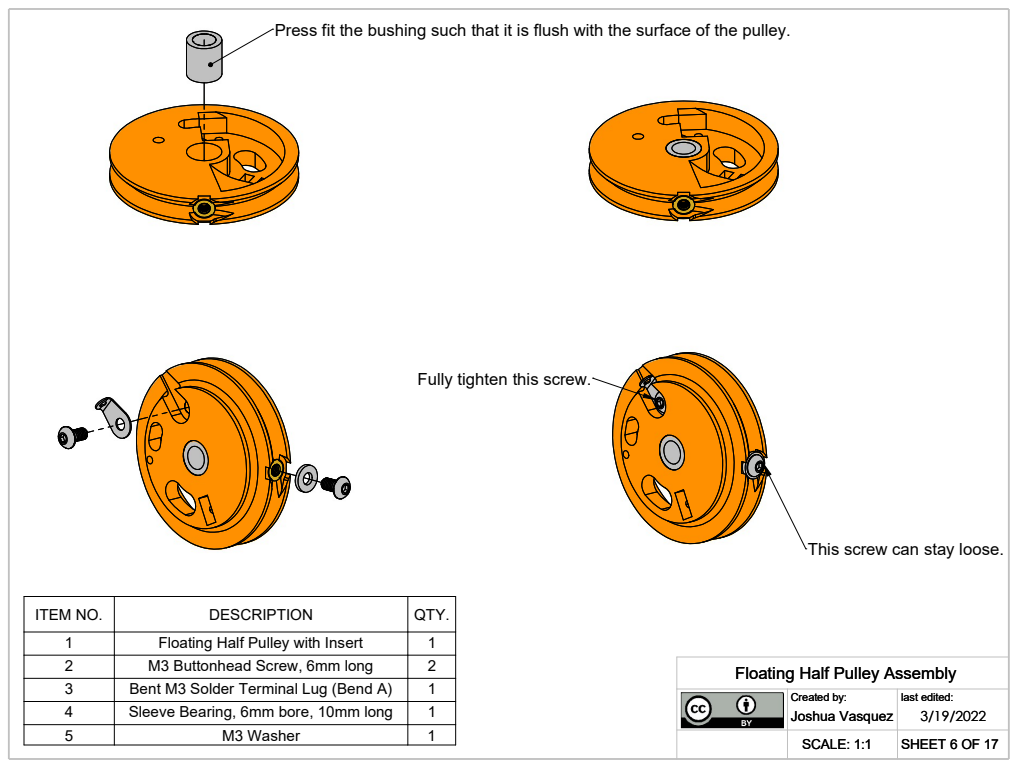
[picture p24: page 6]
M3 Buttonhead Screw, 6mm long

Press fit the bushing such that it is flush with the surface of the pulley.

Fully tighten this screw.

This screw can stay loose.

ITEM NO. | DESCRIPTION | QTY.
1 | Floating Half Pulley with Insert | 1

Floating Half Pulley Assembly

3 | Bent M3 Solder Terminal Lug (Bend A) | 1
4 | Sleeve Bearing, 6mm bore, 10mm long | 1
5 | M3 Washer | 1

Created by: Created by: Joshua Vasquez Joshua Vasquez | last edited: last edited: 3/19/2022

SCALE: 1:1 | SHEET 6 OF 17

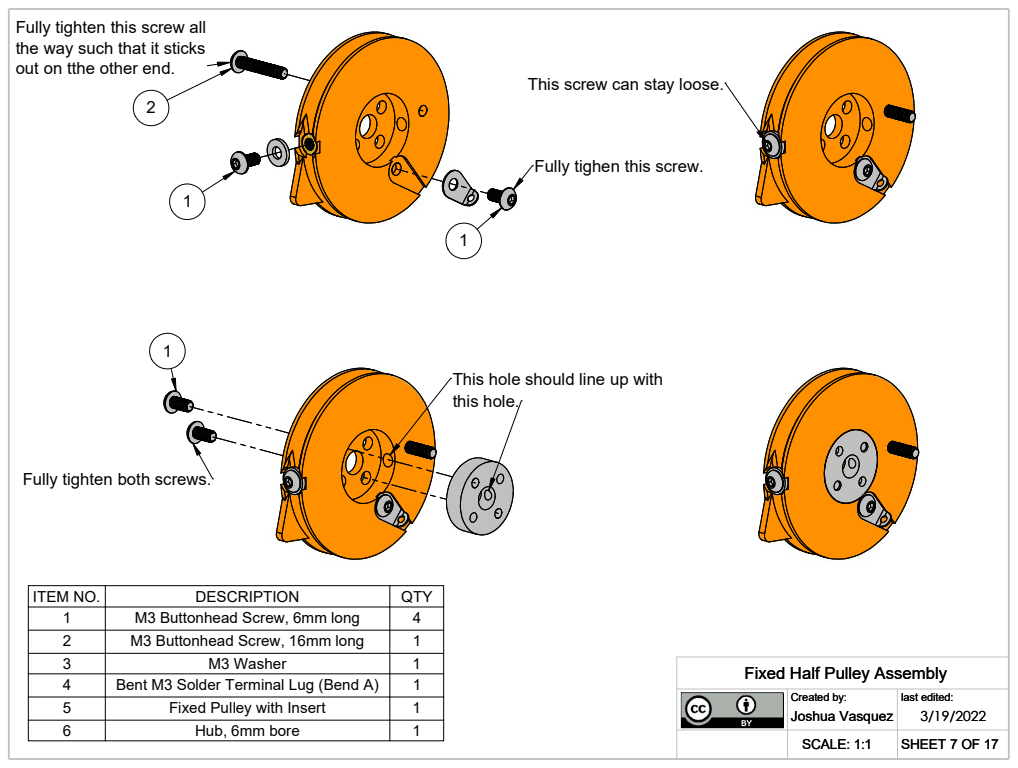
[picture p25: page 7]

Fully tighten this screw all
the way such that it sticks
out on tthe other end.

This screw can stay loose.

Fully tighen this screw.

This hole should line up with
this hole.

Fully tighten both screws.

ITEM NO. | DESCRIPTION | QTY
1 | M3 Buttonhead Screw, 6mm long | 4
2 | M3 Buttonhead Screw, 16mm long | 1
3 | M3 Washer | 1
4 | Bent M3 Solder Terminal Lug (Bend A) | 1
5 | Fixed Pulley with Insert | 1
6 | Hub, 6mm bore | 1

Fixed Half Pulley Assembly

Created by: Created by: Joshua Vasquez Joshua Vasquez | last edited: 3/19/2022 3/19/2022

SCALE: 1:1 | SHEET 7 OF 17

Created by: Joshua Vasquez | last edited: 3/19/2022
SCALE: 1:1 | SHEET 8 OF 17

Wiring

Solder together the folowing limit switch harness. Be sure to insulate the solder connections with heat-shrink tubing.

Note wire lengths with respect to switch buttons.
Note: KK Connectors are included with Duet hardware.

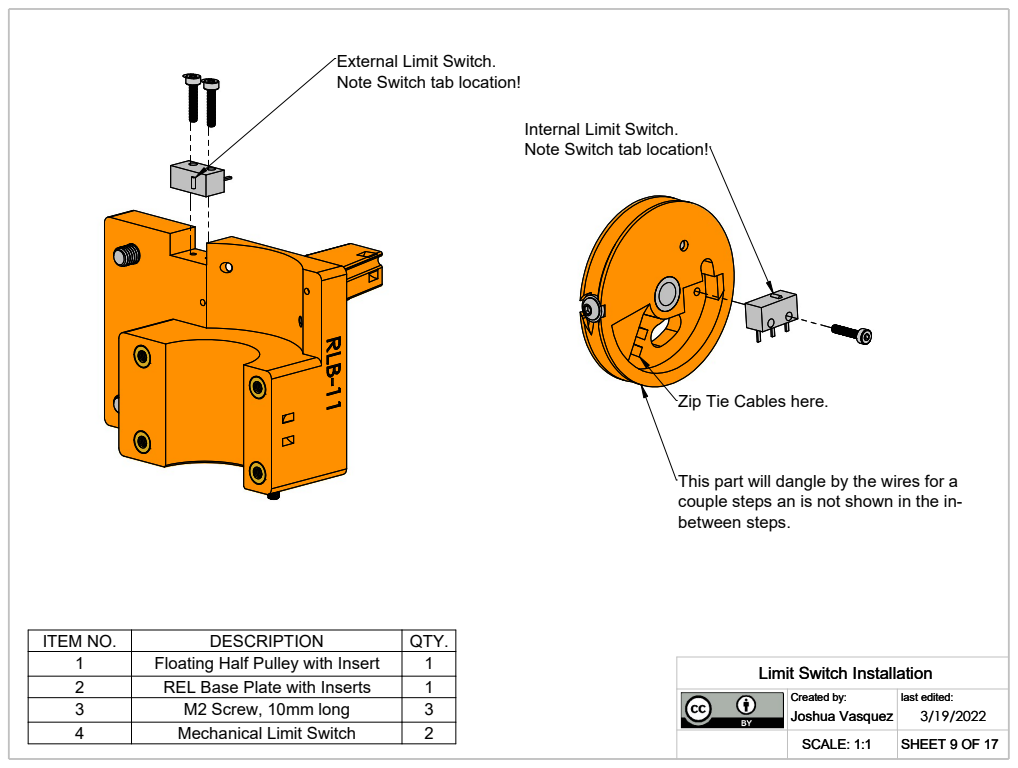
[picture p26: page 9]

External Limit Switch.
Note Switch tab location!

Internal Limit Switch.

Zip Tie Cables here.

This part will dangle by the wires for a
couple steps an is not shown in the in-
between steps.

ITEM NO. | DESCRIPTION | QTY.
1 | Floating Half Pulley with Insert | 1
2 | REL Base Plate with Inserts | 1
3 | M2 Screw, 10mm long | 3
4 | Mechanical Limit Switch | 2

Limit Switch Installation

Created by: Created by: Joshua Vasquez Joshua Vasquez | last edited: last edited: 3/19/2022 3/19/2022

SCALE: 1:1 | SHEET 9 OF 17

B

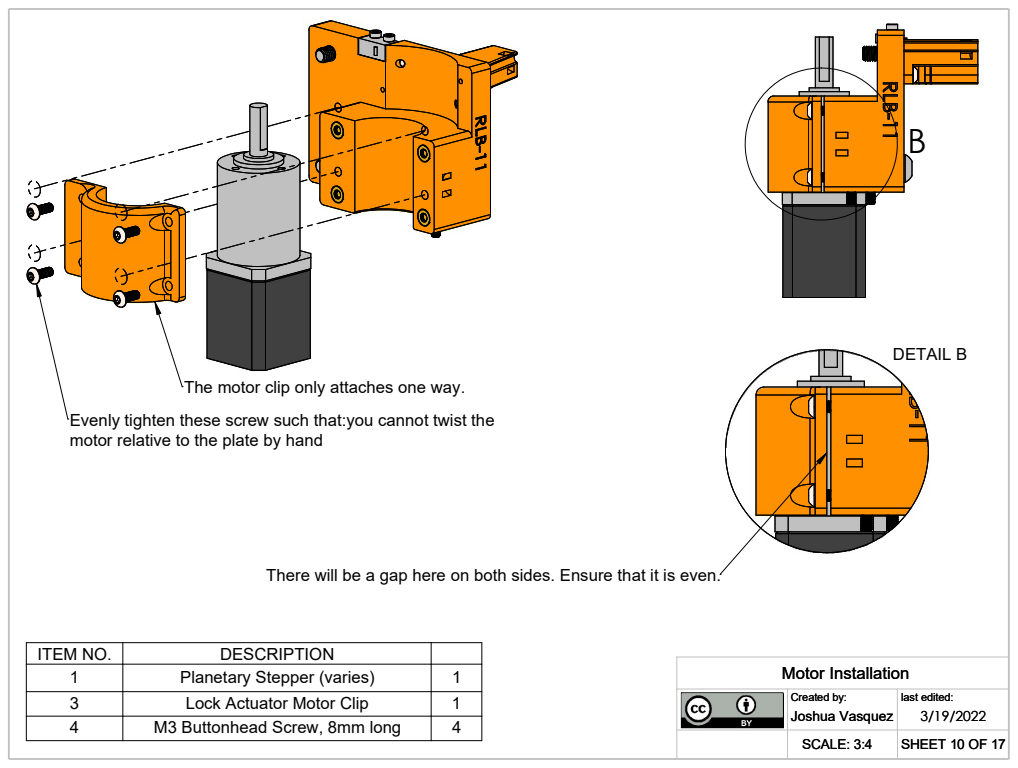
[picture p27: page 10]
SCALE: 3:4; SHEET 10 OF 17; Joshua Vasquez; Created by:; last edited:; Motor Installation; Lock Actuator Motor Clip; M3 Buttonhead Screw, 8mm long; DETAIL B

The motor clip only attaches one way.

Evenly tighten these screw such that:you cannot twist the
motor relative to the plate by hand

There will be a gap here on both sides. Ensure that it is even.

ITEM NO. | DESCRIPTION
1 | Planetary Stepper (varies) | 1

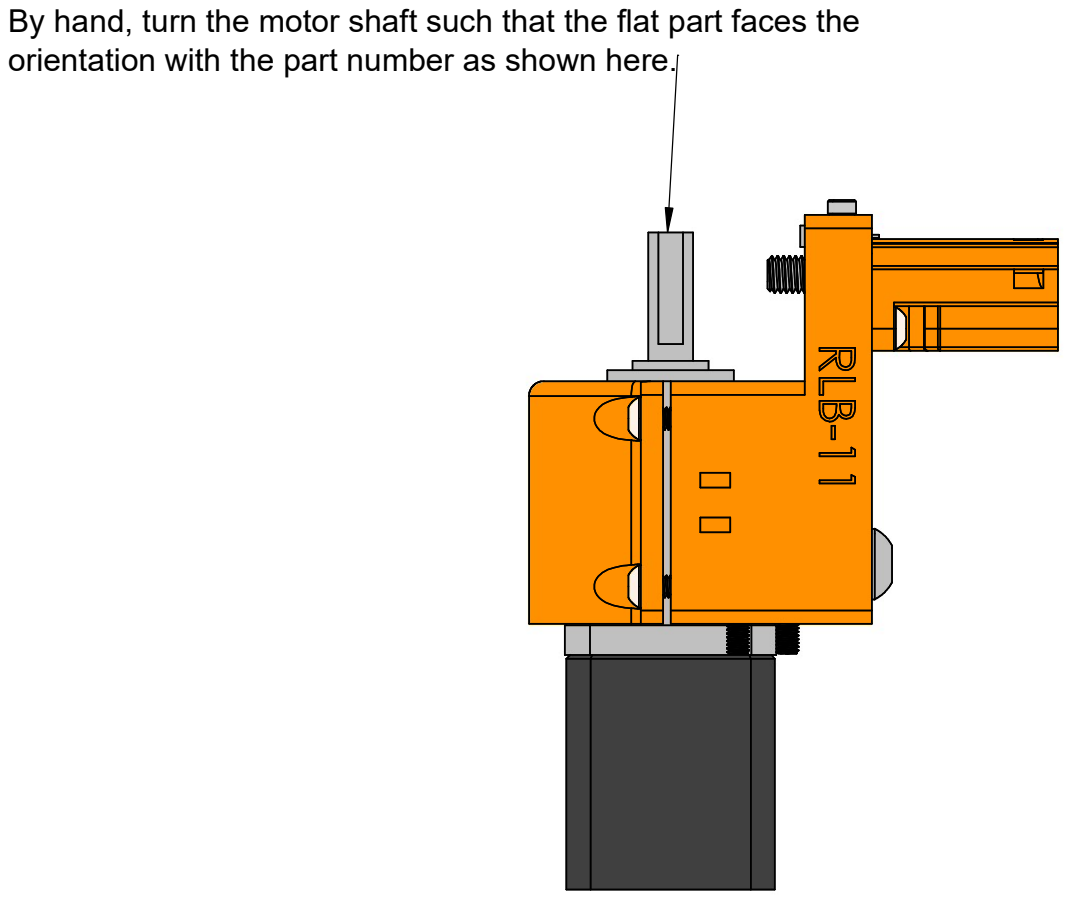
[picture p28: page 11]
Shaft Alignment

By hand, turn the motor shaft such that the flat part faces the
orientation with the part number as shown here.

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

SCALE: 1:1 | SHEET 11 OF 17

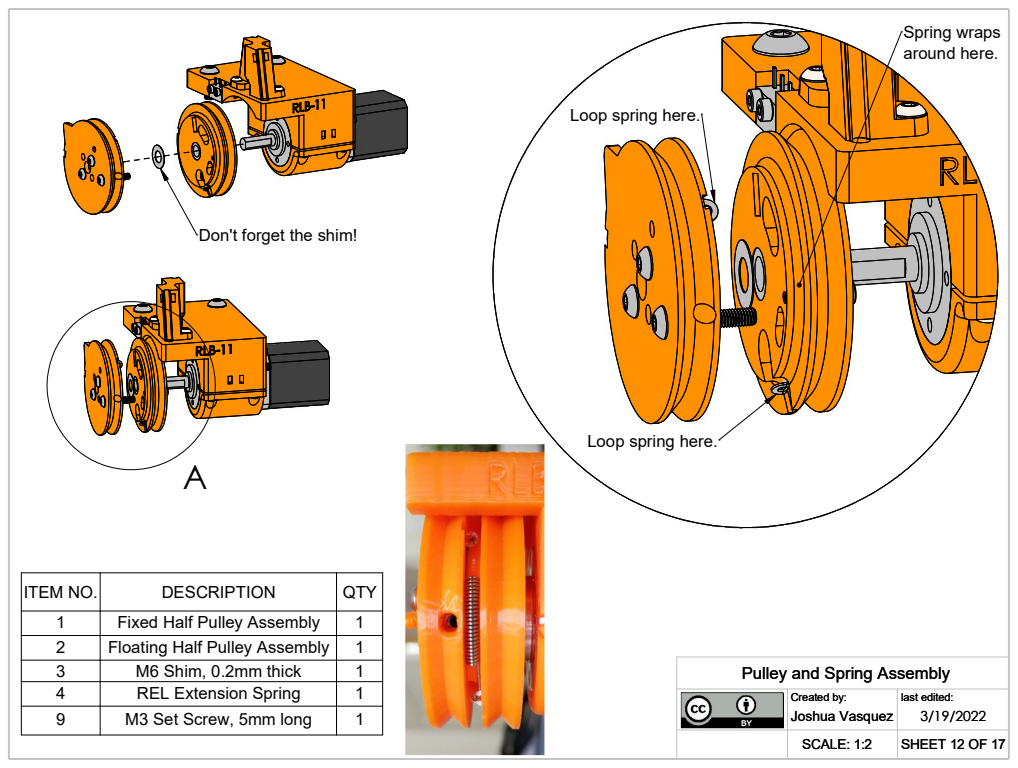
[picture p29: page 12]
M6 Shim, 0.2mm thick; Spring wraps around here.

Loop spring here.

Don't forget the shim!

ITEM NO. | DESCRIPTION | QTY
1 | Fixed Half Pulley Assembly | 1
2 | Floating Half Pulley Assembly | 1

Pulley and Spring Assembly

4 | REL Extension Spring | 1
9 | M3 Set Screw, 5mm long | 1

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

SCALE: 1:2 | SHEET 12 OF 17

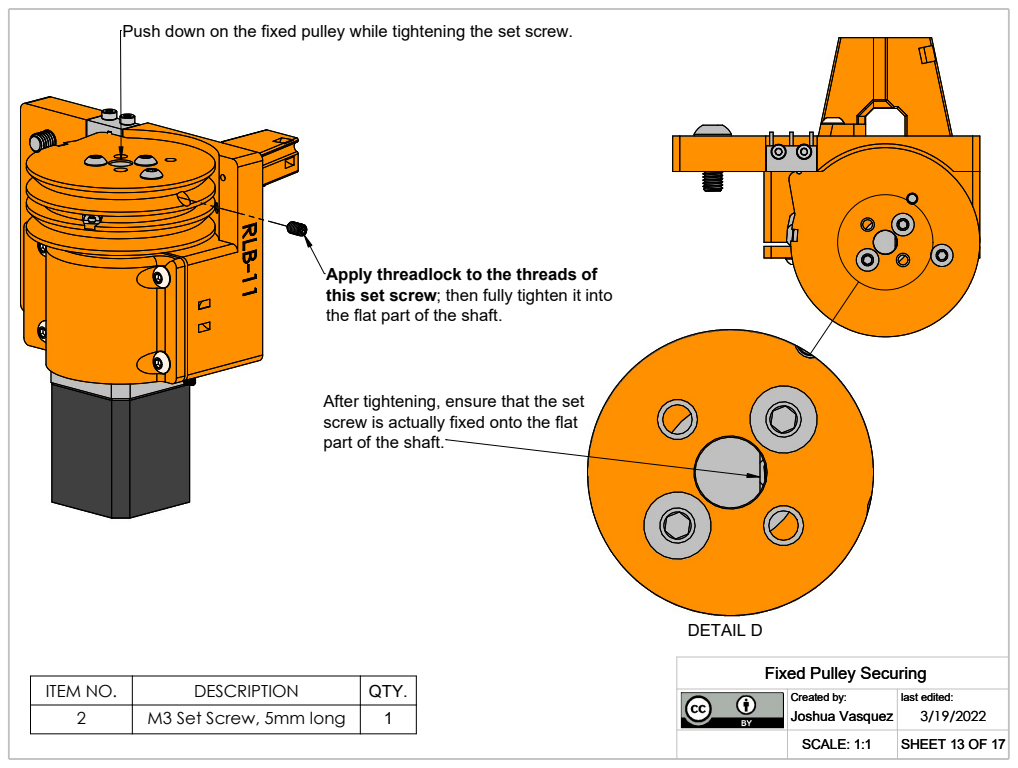
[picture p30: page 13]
DETAIL D

Push down on the fixed pulley while tightening the set screw.

Apply threadlock to the threads of
this set screw; then fully tighten it into
the flat part of the shaft.

After tightening, ensure that the set
screw is actually fixed onto the flat
part of the shaft.

Fixed Pulley Securing

ITEM NO. | DESCRIPTION | QTY.
2 | M3 Set Screw, 5mm long | 1

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

SCALE: 1:1 | SHEET 13 OF 17

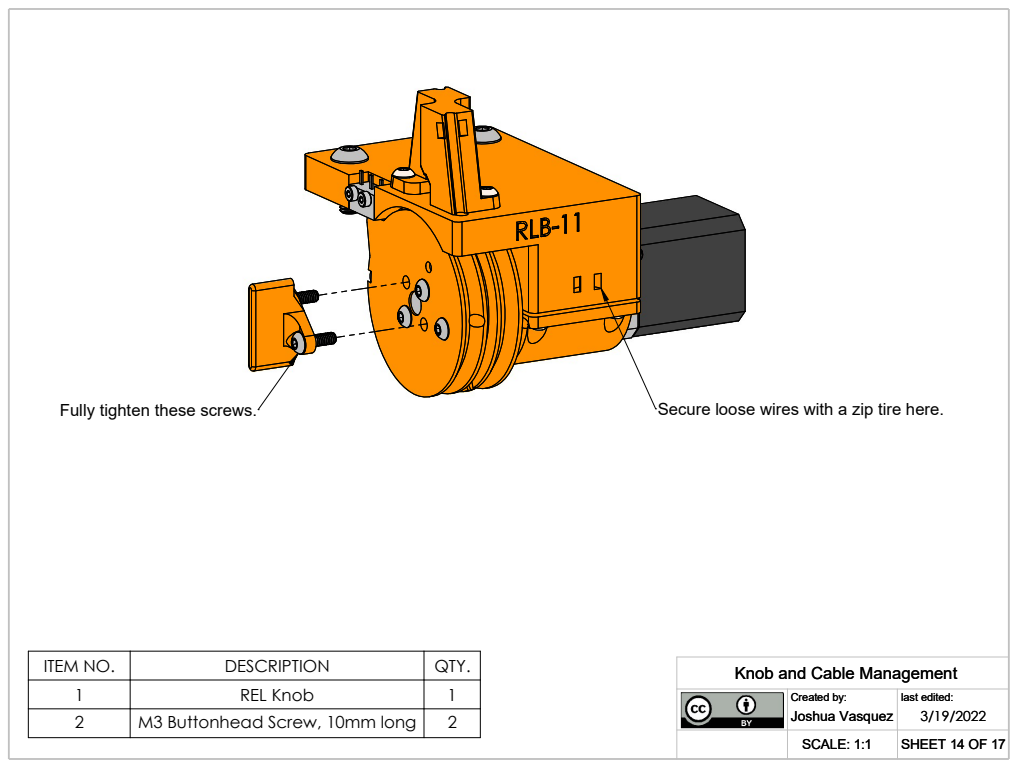
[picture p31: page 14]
Fully tighten these screws.; Secure loose wires with a zip tire here.

ITEM NO. | DESCRIPTION | QTY.
1 | REL Knob | 1
2 | M3 Buttonhead Screw, 10mm long | 2

Knob and Cable Management

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

SCALE: 1:1 | SHEET 14 OF 17

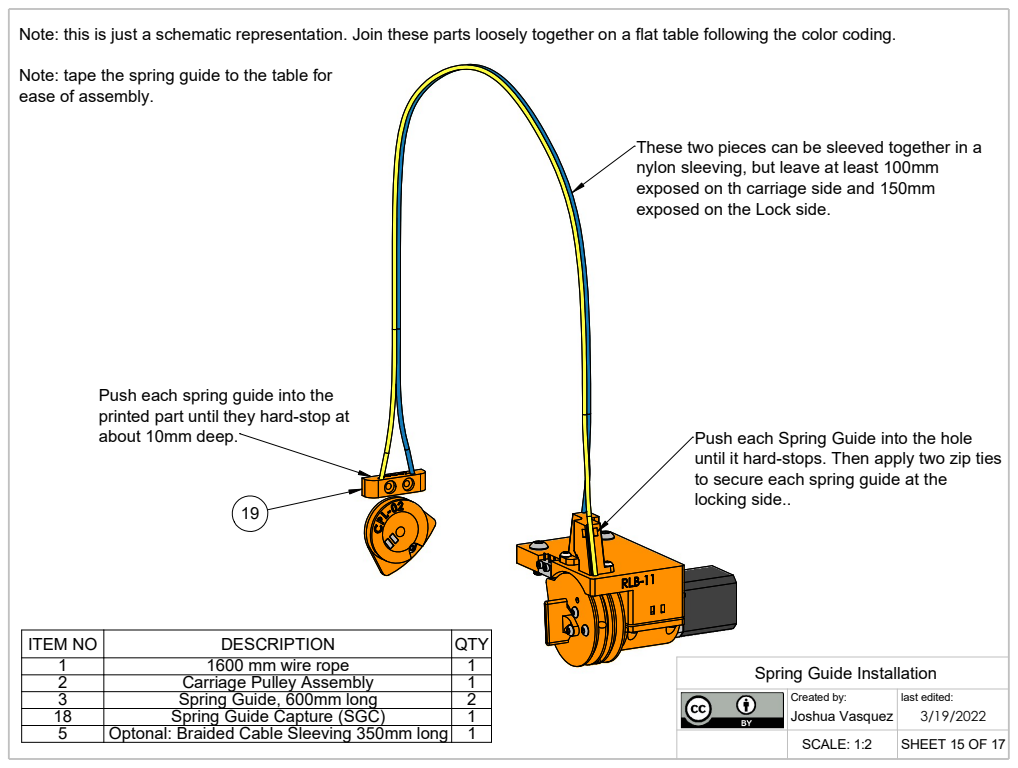
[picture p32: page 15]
Joshua Vasquez; Created by:; last edited:; ITEM NO; DESCRIPTION; QTY; 1600 mm wire rope; Carriage Pulley Assembly; Spring Guide, 600mm long

Note: this is just a schematic representation. Join these parts loosely together on a flat table following the color coding.

Note: tape the spring guide to the table for
ease of assembly.

These two pieces can be sleeved together in a
nylon sleeving, but leave at least 100mm
exposed on th carriage side and 150mm
exposed on the Lock side.

Push each spring guide into the
printed part until they hard-stop at
about 10mm deep.

Push each Spring Guide into the hole
until it hard-stops. Then apply two zip ties
to secure each spring guide at the
locking side..

Spring Guide Installation

18 | Spring Guide Capture (SGC) | 1
5 | Optonal: Braided Cable Sleeving 350mm long | 1

SCALE: 1:2 | SHEET 15 OF 17

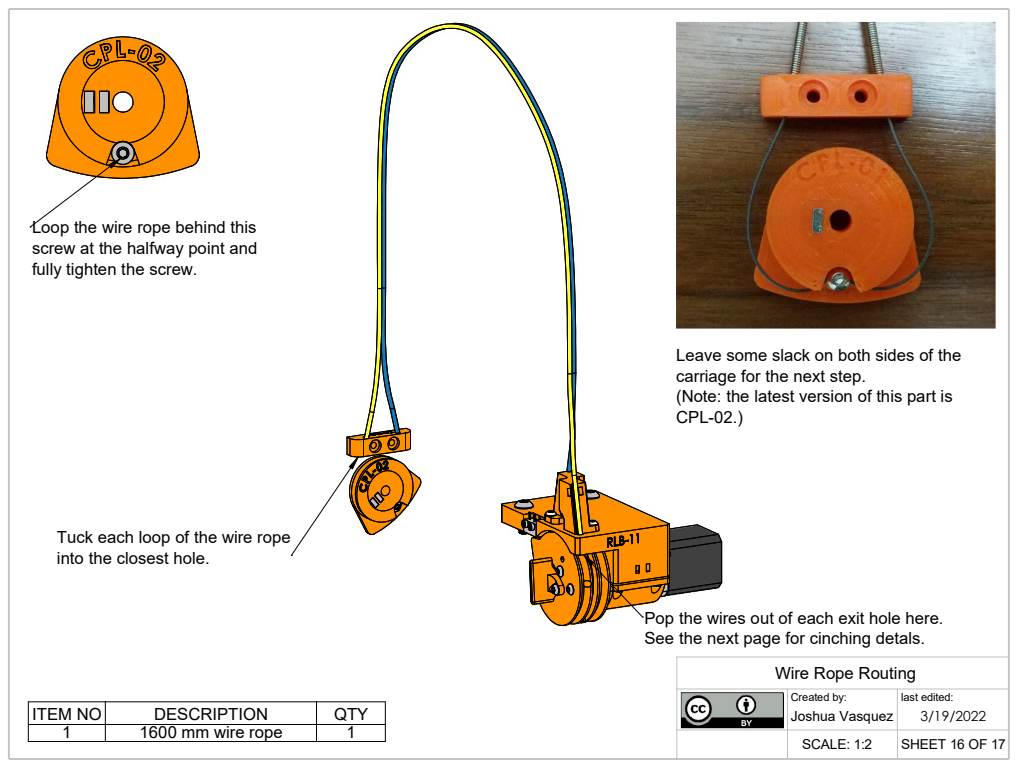
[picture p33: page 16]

Loop the wire rope behind this
screw at the halfway point and
fully tighten the screw.

Leave some slack on both sides of the
carriage for the next step.
(Note: the latest version of this part is
CPL-02.)

Tuck each loop of the wire rope
into the closest hole.

Pop the wires out of each exit hole here.
See the next page for cinching detals.

Wire Rope Routing

Created by: Joshua Vasquez | last edited: 3/19/2022

ITEM NO | DESCRIPTION | QTY
1 | 1600 mm wire rope | 1

SCALE: 1:2 | SHEET 16 OF 17

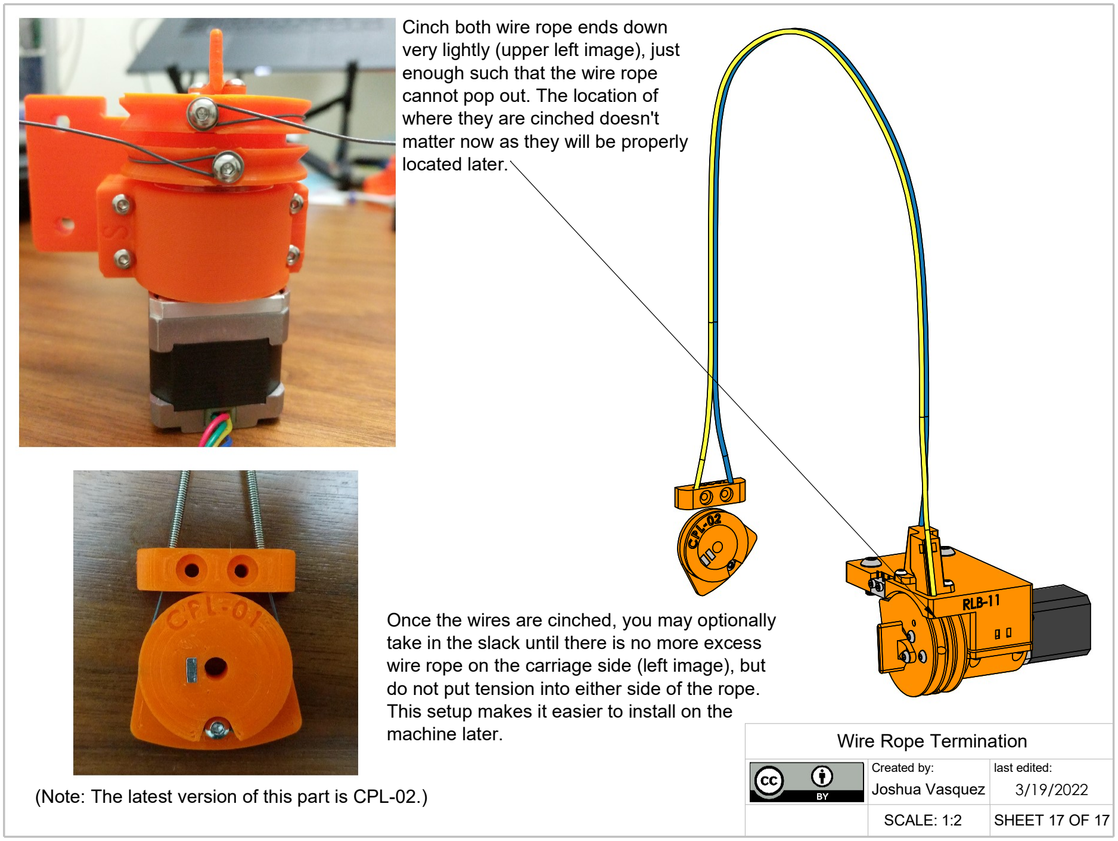
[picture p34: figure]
SCALE: 1:2; SHEET 17 OF 17; Created by: Joshua Vasquez; last edited: 3/19/2022; Wire Rope Termination; machine later.; Cinch both wire rope ends down very lightly (upper left image), just enough such that the wire rope cannot pop out. The location of where they are cinched doesn't matter now as they will be properly located later.

Once the wires are cinched, you may optionally take in the slack until there is no more excess wire rope on the carriage side (left image), but do not put tension into either side of the rope. This setup makes it easier to install on the

(Note: The latest version of this part is CPL-02.)

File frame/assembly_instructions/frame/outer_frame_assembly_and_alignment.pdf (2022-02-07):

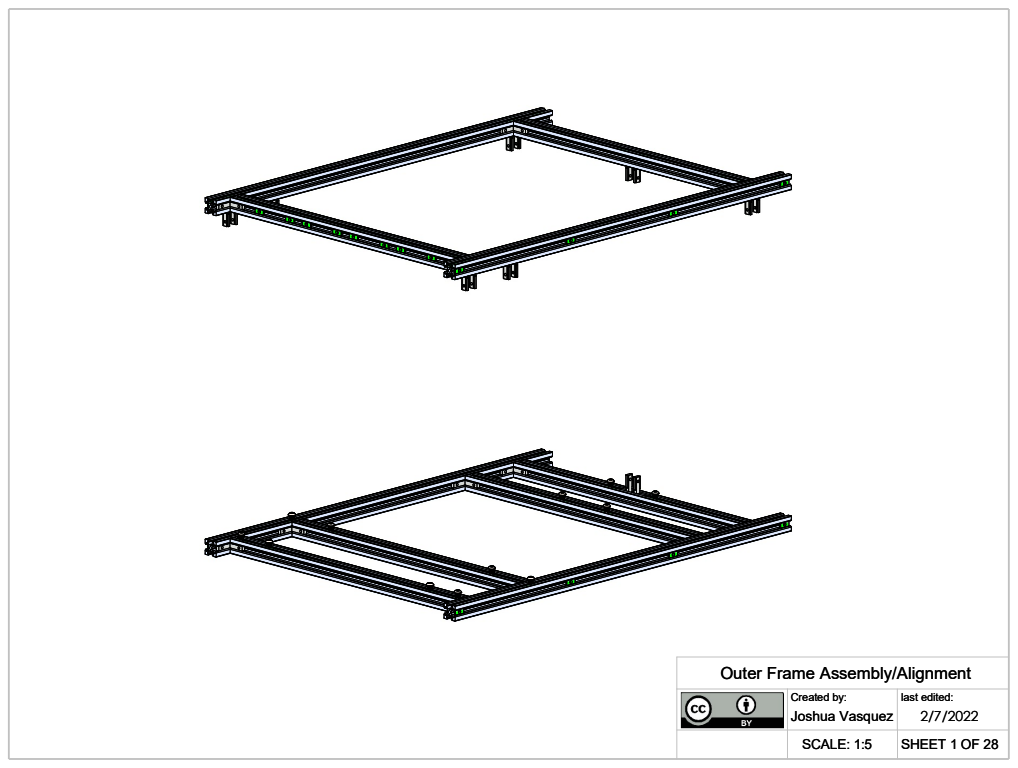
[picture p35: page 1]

Outer Frame Assembly/Alignment

Created by: Created by: Joshua Vasquez Joshua Vasquez | last edited: last edited: 2/7/2022 2/7/2022

SCALE: 1:5 | SHEET 1 OF 28

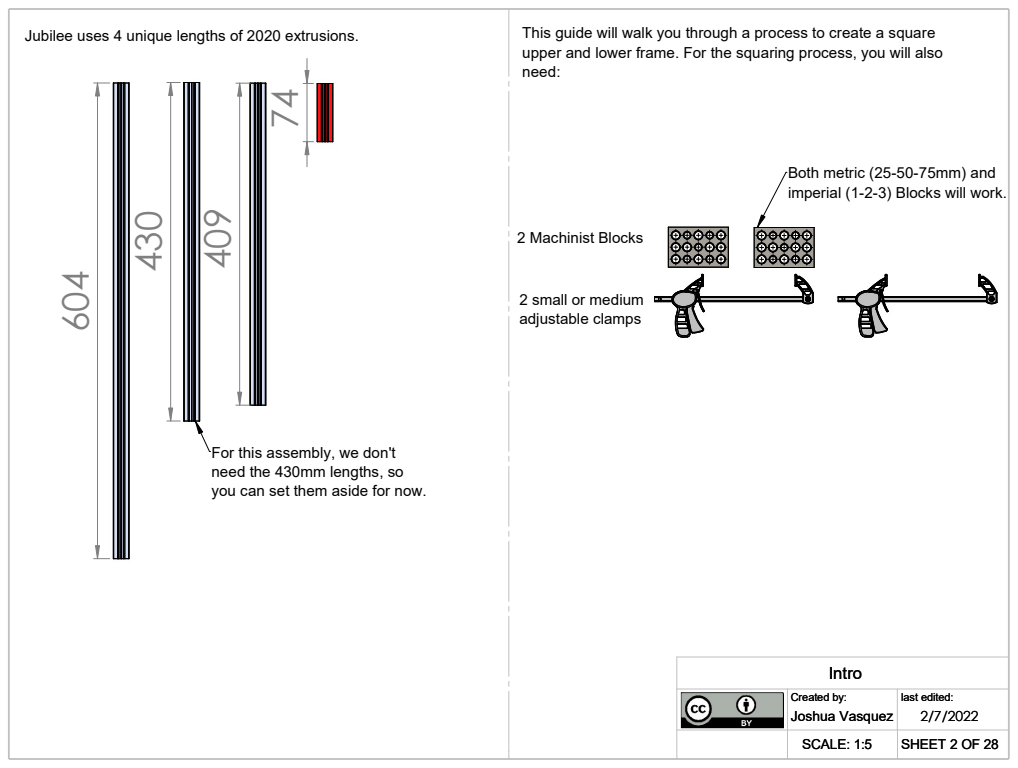
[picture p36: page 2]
Intro; imperial (1-2-3) Blocks will work. 409; Jubilee uses 4 unique lengths of 2020 extrusions.; This guide will walk you through a process to create a square; 2 Machinist Blocks; 2 small or medium 604; adjustable clamps

upper and lower frame. For the squaring process, you will also
need:

Both metric (25-50-75mm) and

you can set them aside for now. 430

For this assembly, we don't
need the 430mm lengths, so

Created by: Created by: Joshua Vasquez Joshua Vasquez | last edited: last edited: 2/7/2022 2/7/2022

SCALE: 1:5 | SHEET 2 OF 28

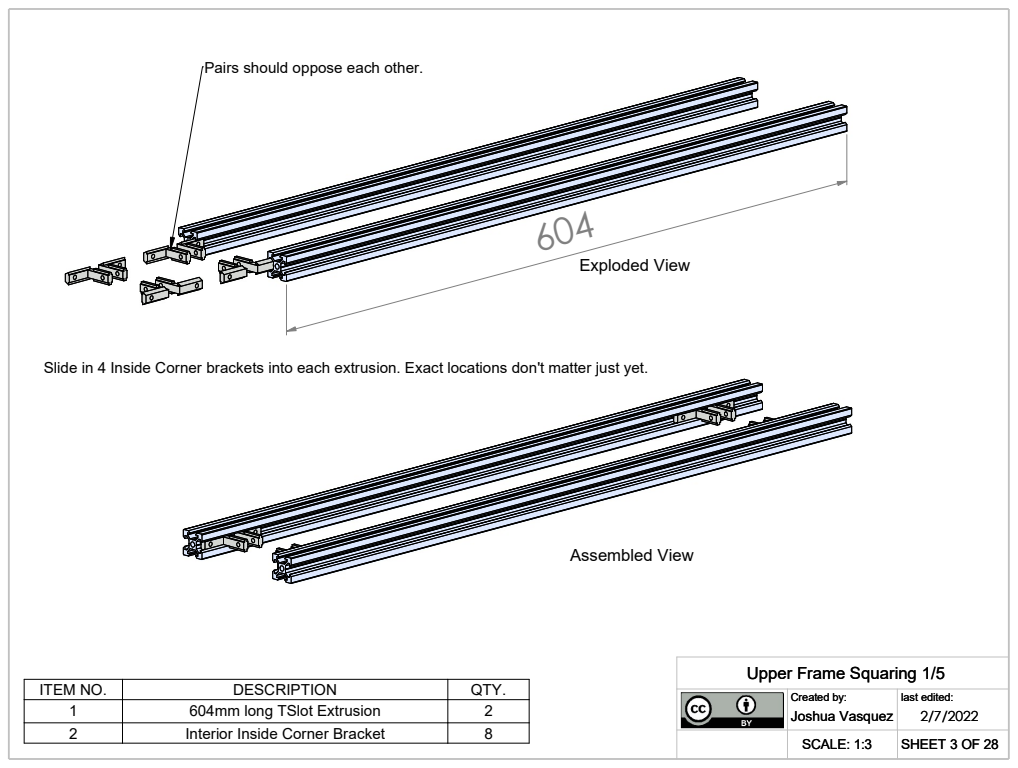
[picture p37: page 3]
Exploded View; Assembled View

Pairs should oppose each other.

Slide in 4 Inside Corner brackets into each extrusion. Exact locations don't matter just yet.

Upper Frame Squaring 1/5

ITEM NO. | DESCRIPTION | QTY.
1 | 604mm long TSlot Extrusion | 2
2 | Interior Inside Corner Bracket | 8

Created by: Created by: Joshua Vasquez Joshua Vasquez | last edited: last edited: 2/7/2022 2/7/2022

SCALE: 1:3 | SHEET 3 OF 28

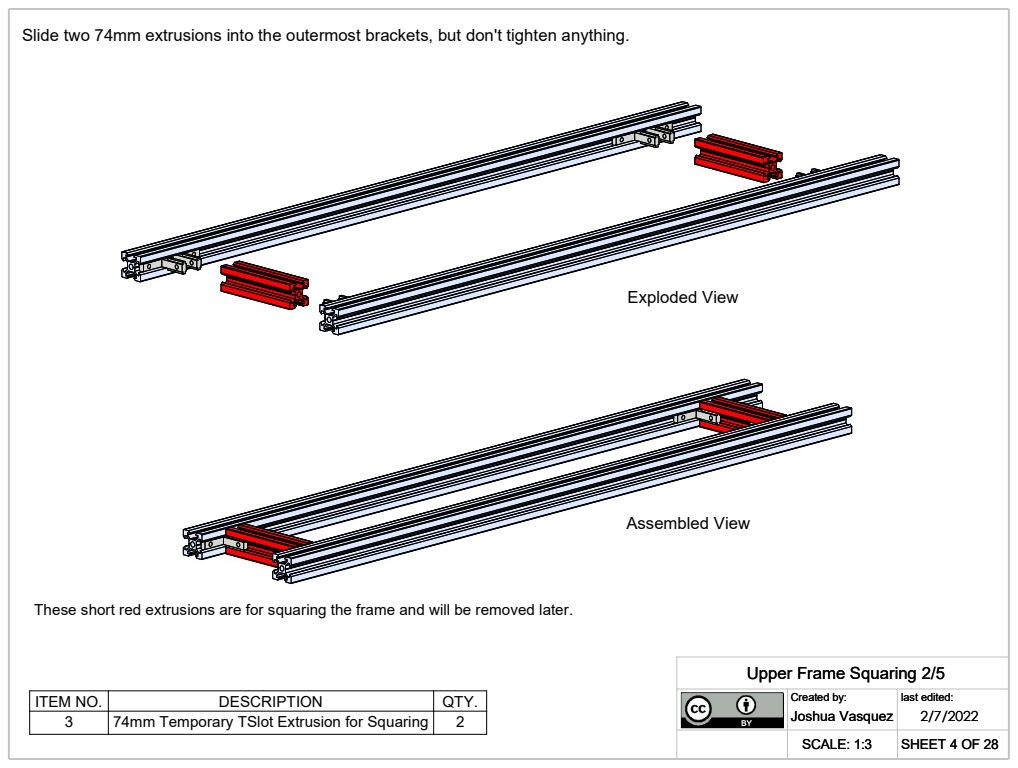
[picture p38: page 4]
Joshua Vasquez; Created by:; last edited:; Assembled View; ITEM NO.; DESCRIPTION; QTY.; Exploded View

Slide two 74mm extrusions into the outermost brackets, but don't tighten anything.

These short red extrusions are for squaring the frame and will be removed later.

Upper Frame Squaring 2/5

3 | 74mm Temporary TSlot Extrusion for Squaring | 2

SCALE: 1:3 | SHEET 4 OF 28

Slide two Machinist Blocks into the frame on both ends and gently clamp the entire setup together as shown below.

Push the Blocks into the short extrusions on both sides.

Note that the red extrusions will be loose. This is intentional. In this configuration, the frame is
"square" using the 1-2-3 Blocks as a reference.

Upper Frame Squaring 3/5

ITEM NO. | DESCRIPTION | QTY.
3 | 25-50-75mm (or 1-2-3) Machinist Block | 2
4 | Adjustable Clamp | 2

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

SCALE: 1:3 | SHEET 5 OF 28

Using Calipers or a ruler as a reference, set the short extrusions such that they match the dimensions shown above. The Blocks should
still be touching. When the dimensions are set, clamp firmly.

Upper Frame Squaring 4/5

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

SCALE: 1:3 | SHEET 6 OF 28

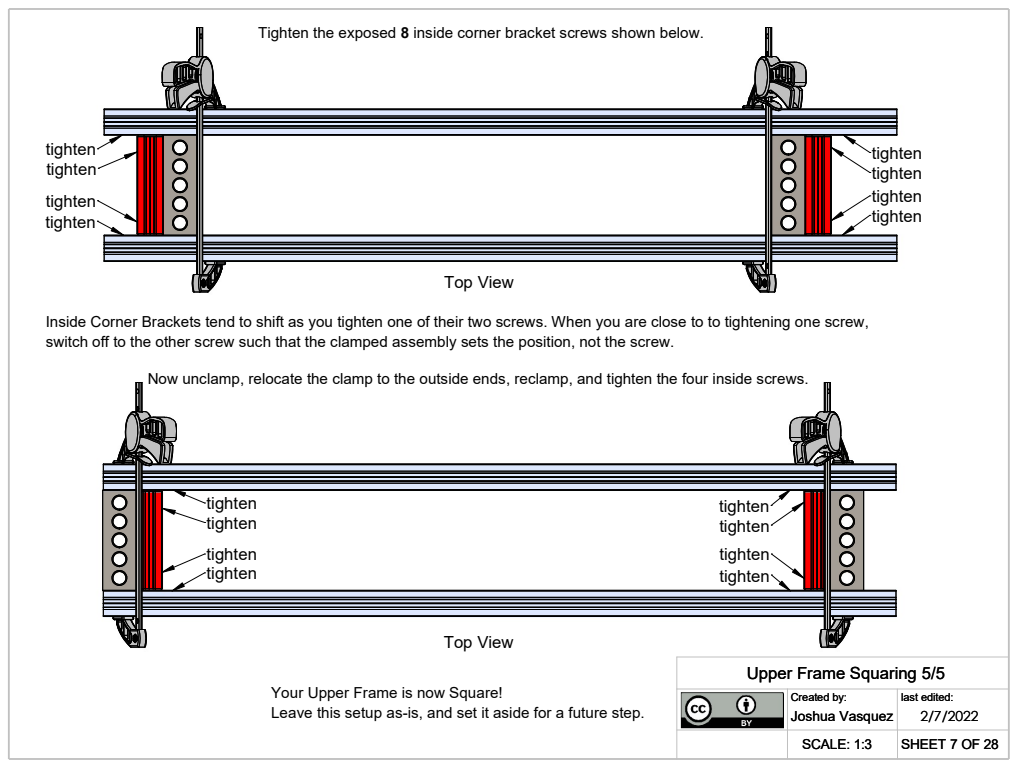
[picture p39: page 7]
Top View; tighten tighten; tighten tighten tighten tighten

Tighten the exposed 8 inside corner bracket screws shown below.

Inside Corner Brackets tend to shift as you tighten one of their two screws. When you are close to to tightening one screw,
switch off to the other screw such that the clamped assembly sets the position, not the screw.

Now unclamp, relocate the clamp to the outside ends, reclamp, and tighten the four inside screws.

Upper Frame Squaring 5/5

Your Upper Frame is now Square!
Leave this setup as-is, and set it aside for a future step.

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

SCALE: 1:3 | SHEET 7 OF 28

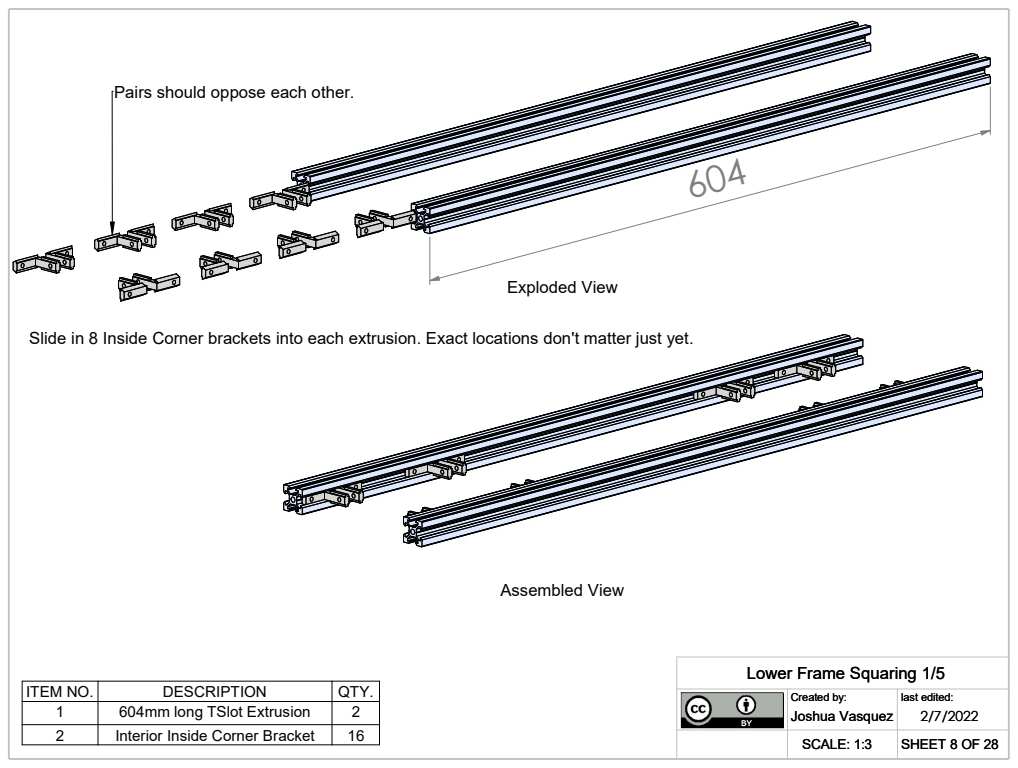
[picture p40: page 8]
Assembled View; Exploded View

Pairs should oppose each other.

Slide in 8 Inside Corner brackets into each extrusion. Exact locations don't matter just yet.

Lower Frame Squaring 1/5

ITEM NO. | DESCRIPTION | QTY.
1 | 604mm long TSlot Extrusion | 2
2 | Interior Inside Corner Bracket | 16

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

SCALE: 1:3 | SHEET 8 OF 28

Slide two 74mm extrusions into the outermost brackets, but don't tighten anything.

Lower Frame Squaring 2/5

ITEM NO. | DESCRIPTION | QTY.
1 | 74mm Temporary TSlot Extrusion for Squaring | 2

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

SCALE: 1:3 | SHEET 9 OF 28

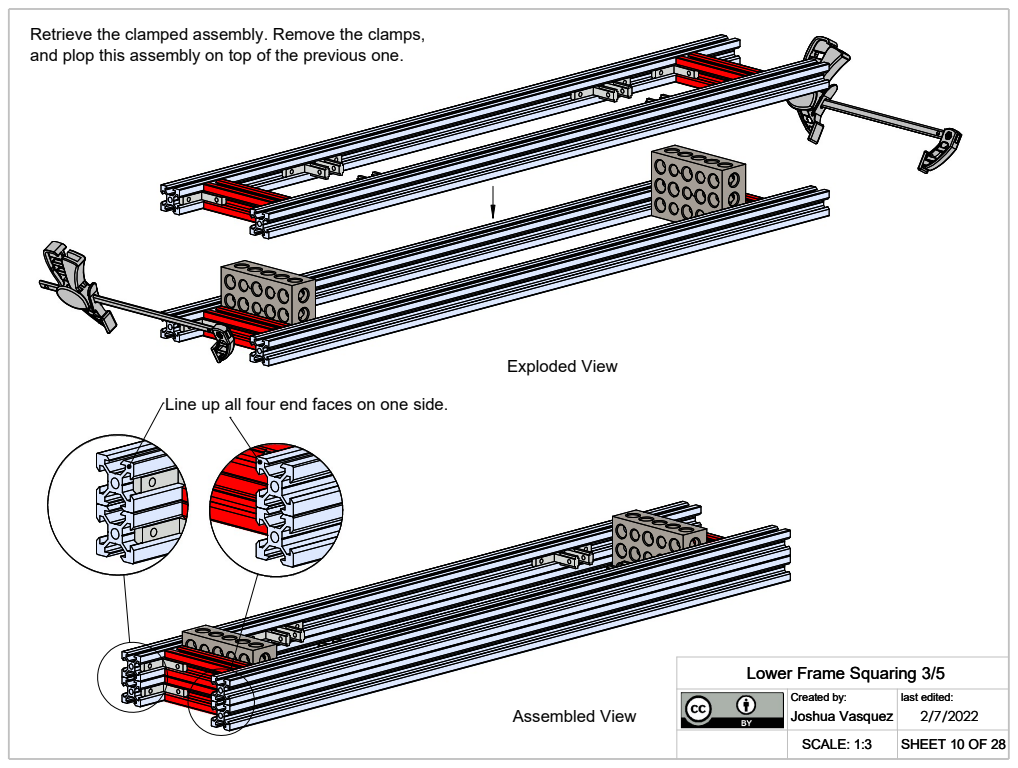
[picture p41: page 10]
Assembled View; Exploded View

Retrieve the clamped assembly. Remove the clamps,
and plop this assembly on top of the previous one.

Line up all four end faces on one side.

Lower Frame Squaring 3/5

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

SCALE: 1:3 | SHEET 10 OF 28

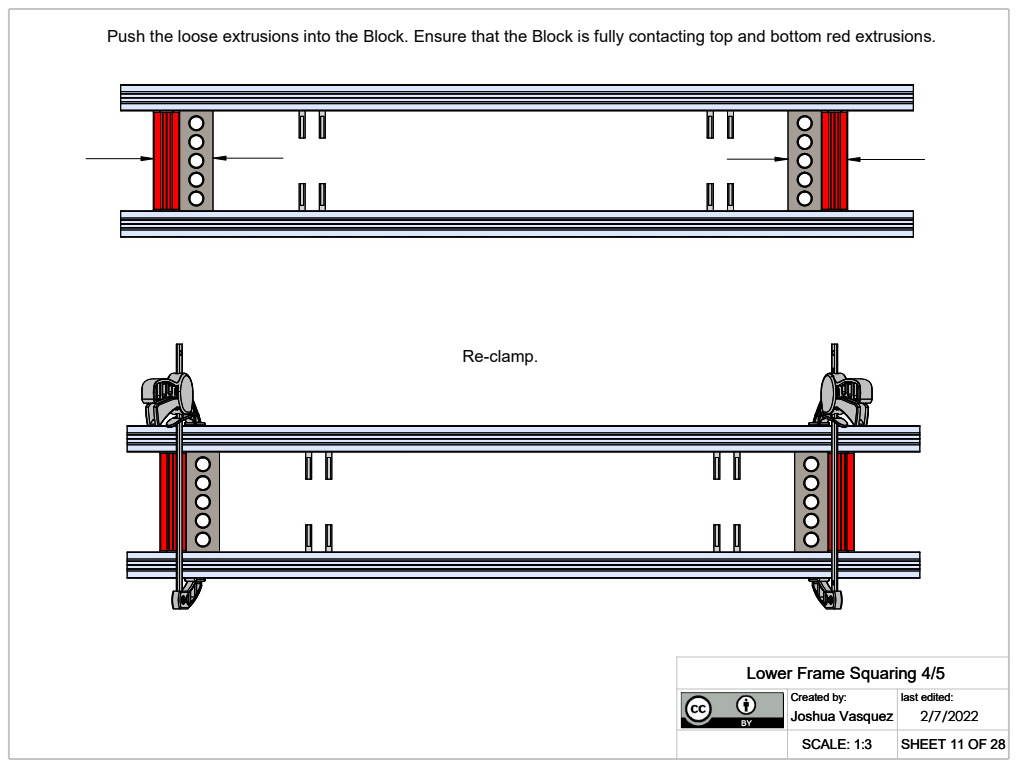
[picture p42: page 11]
Re-clamp.

Push the loose extrusions into the Block. Ensure that the Block is fully contacting top and bottom red extrusions.

Lower Frame Squaring 4/5

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

SCALE: 1:3 | SHEET 11 OF 28

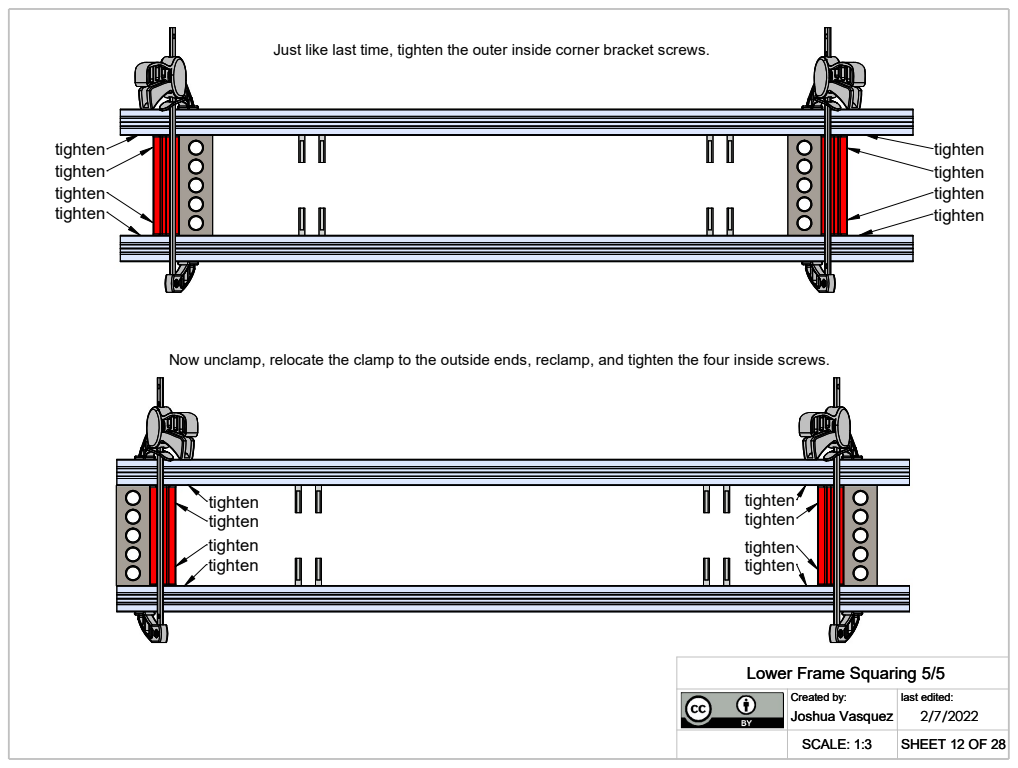
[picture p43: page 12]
tighten tighten tighten tighten; tighten tighten

Just like last time, tighten the outer inside corner bracket screws.

Now unclamp, relocate the clamp to the outside ends, reclamp, and tighten the four inside screws.

Lower Frame Squaring 5/5

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

SCALE: 1:3 | SHEET 12 OF 28

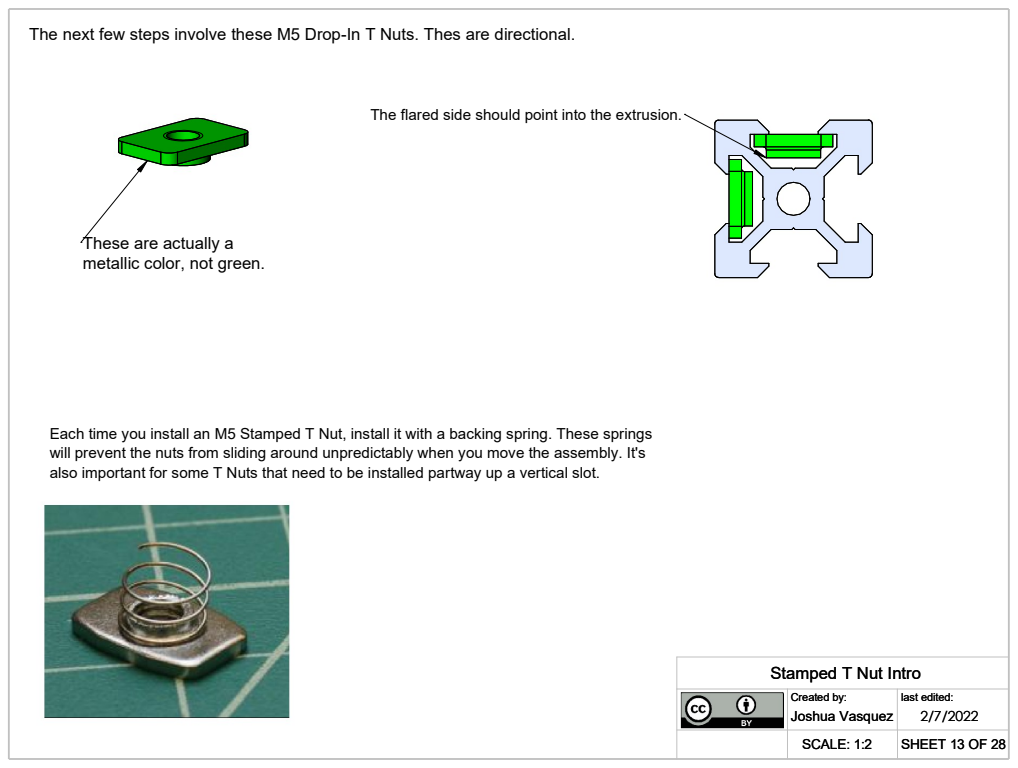
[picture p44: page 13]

The next few steps involve these M5 Drop-In T Nuts. Thes are directional.

The flared side should point into the extrusion.

These are actually a
metallic color, not green.

Each time you install an M5 Stamped T Nut, install it with a backing spring. These springs
will prevent the nuts from sliding around unpredictably when you move the assembly. It's
also important for some T Nuts that need to be installed partway up a vertical slot.

Stamped T Nut Intro

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

SCALE: 1:2 | SHEET 13 OF 28

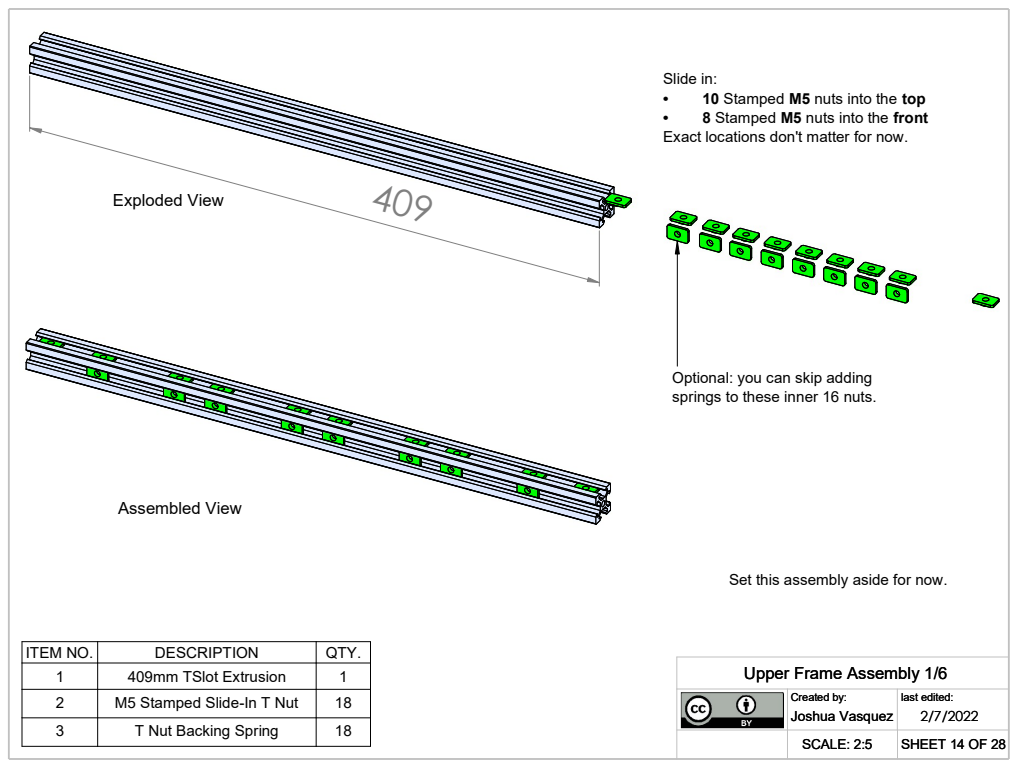
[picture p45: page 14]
SCALE: 2:5; SHEET 14 OF 28; Joshua Vasquez; Created by:; last edited:; Exploded View; M5 Stamped Slide-In T Nut; T Nut Backing Spring; Assembled View

Slide in:
• 10 Stamped M5 nuts into the top
• 8 Stamped M5 nuts into the front
Exact locations don't matter for now.

Optional: you can skip adding
springs to these inner 16 nuts.

Set this assembly aside for now.

ITEM NO. | DESCRIPTION | QTY.
1 | 409mm TSlot Extrusion | 1

Upper Frame Assembly 1/6

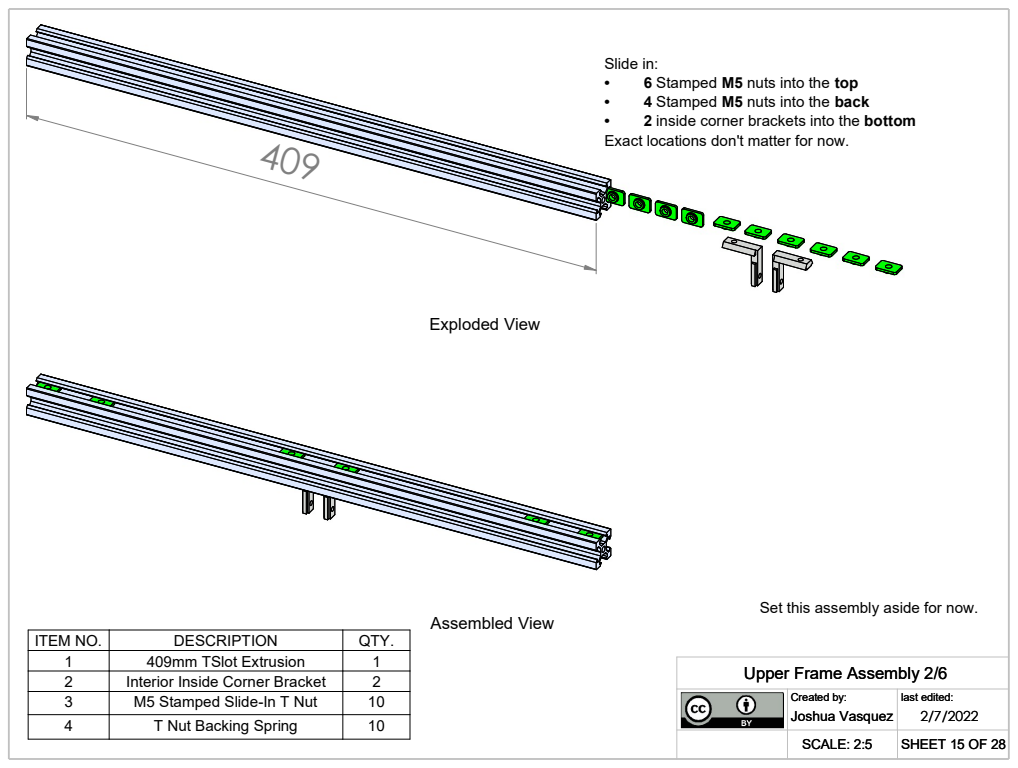
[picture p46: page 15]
SCALE: 2:5; SHEET 15 OF 28; Joshua Vasquez; Created by:; last edited:; Assembled View; M5 Stamped Slide-In T Nut; T Nut Backing Spring; Exploded View

Slide in:
• 6 Stamped M5 nuts into the top
• 4 Stamped M5 nuts into the back
• 2 inside corner brackets into the bottom
Exact locations don't matter for now.

Set this assembly aside for now.

ITEM NO. | DESCRIPTION | QTY.
1 | 409mm TSlot Extrusion | 1
2 | Interior Inside Corner Bracket | 2

Upper Frame Assembly 2/6

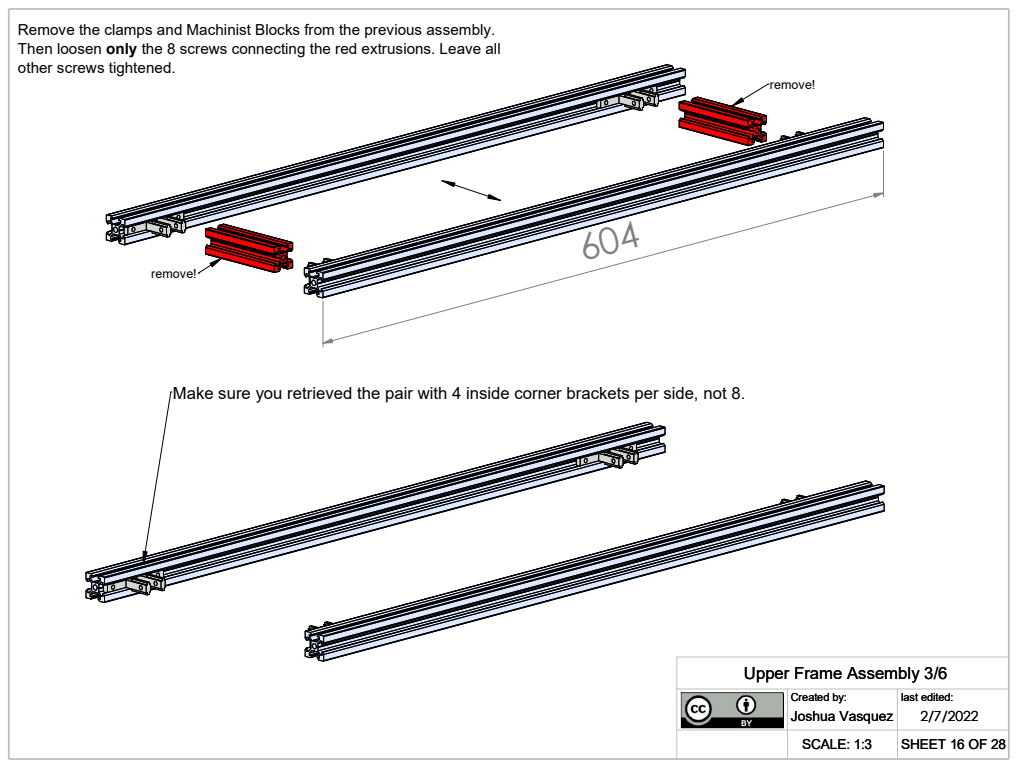
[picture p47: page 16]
remove!

Remove the clamps and Machinist Blocks from the previous assembly.
Then loosen only the 8 screws connecting the red extrusions. Leave all
other screws tightened.

Make sure you retrieved the pair with 4 inside corner brackets per side, not 8.

Upper Frame Assembly 3/6

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

SCALE: 1:3 | SHEET 16 OF 28

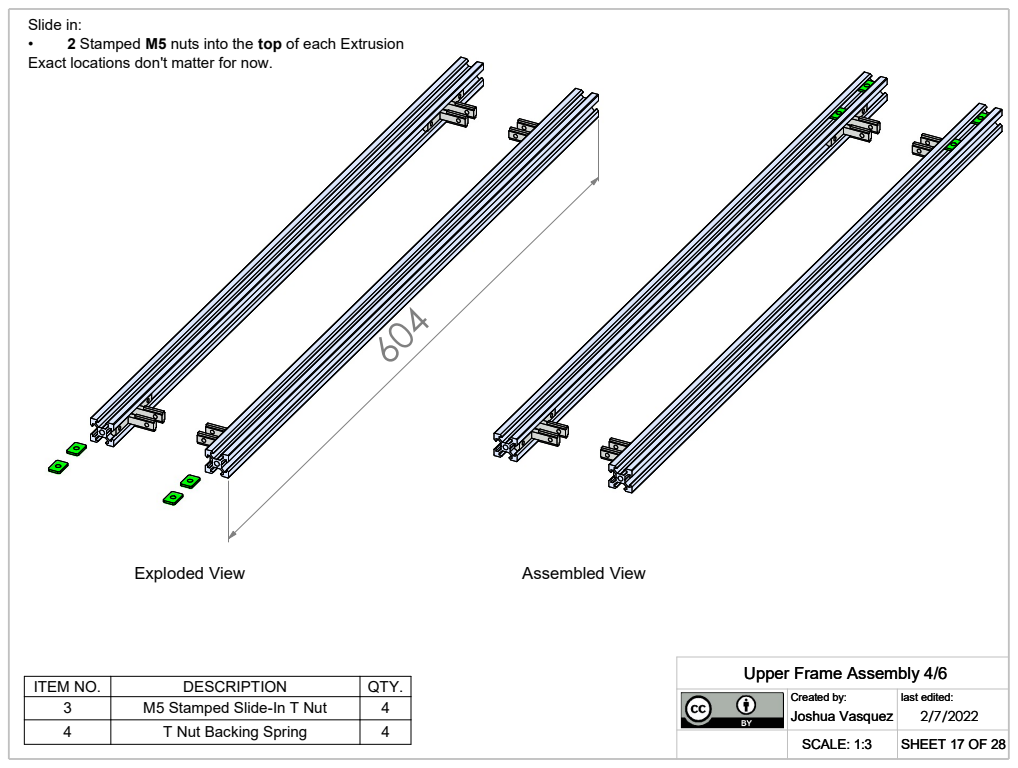
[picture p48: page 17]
Exploded View; Assembled View

Slide in:
• 2 Stamped M5 nuts into the top of each Extrusion
Exact locations don't matter for now.

Upper Frame Assembly 4/6

ITEM NO. | DESCRIPTION | QTY.
3 | M5 Stamped Slide-In T Nut | 4
4 | T Nut Backing Spring | 4

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

SCALE: 1:3 | SHEET 17 OF 28

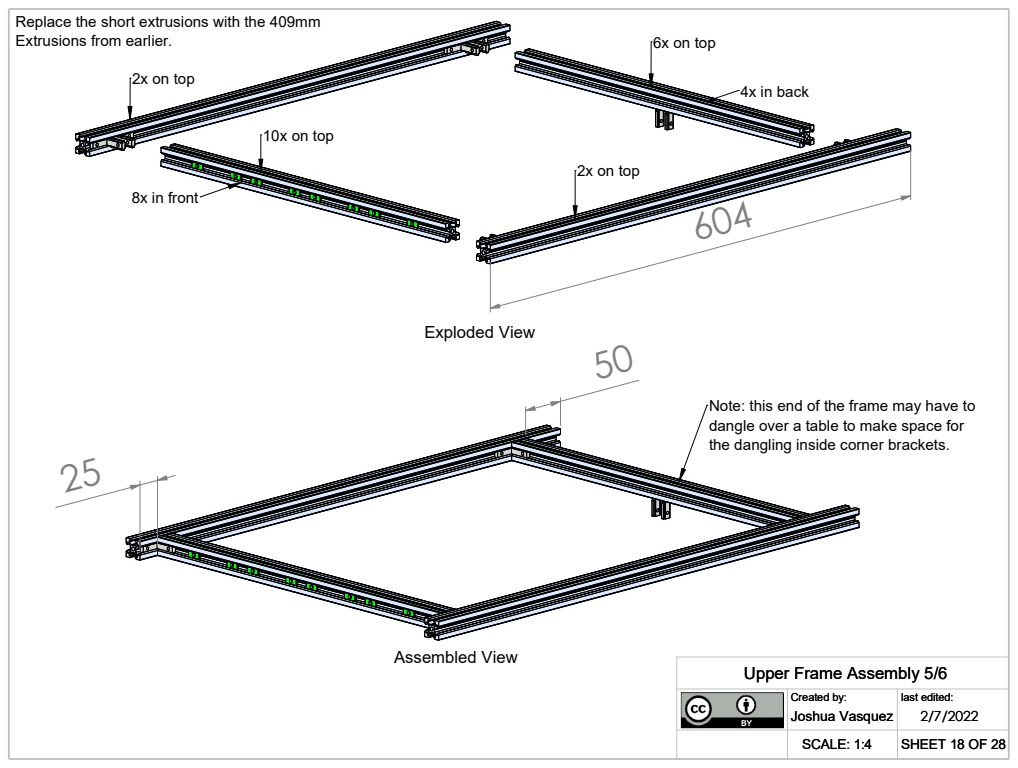
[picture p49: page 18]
Assembled View; Exploded View; 8x in front; 10x on top; 4x in back; 6x on top; 2x on top

Replace the short extrusions with the 409mm
Extrusions from earlier.

Note: this end of the frame may have to
dangle over a table to make space for
the dangling inside corner brackets.

Upper Frame Assembly 5/6

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

SCALE: 1:4 | SHEET 18 OF 28

L

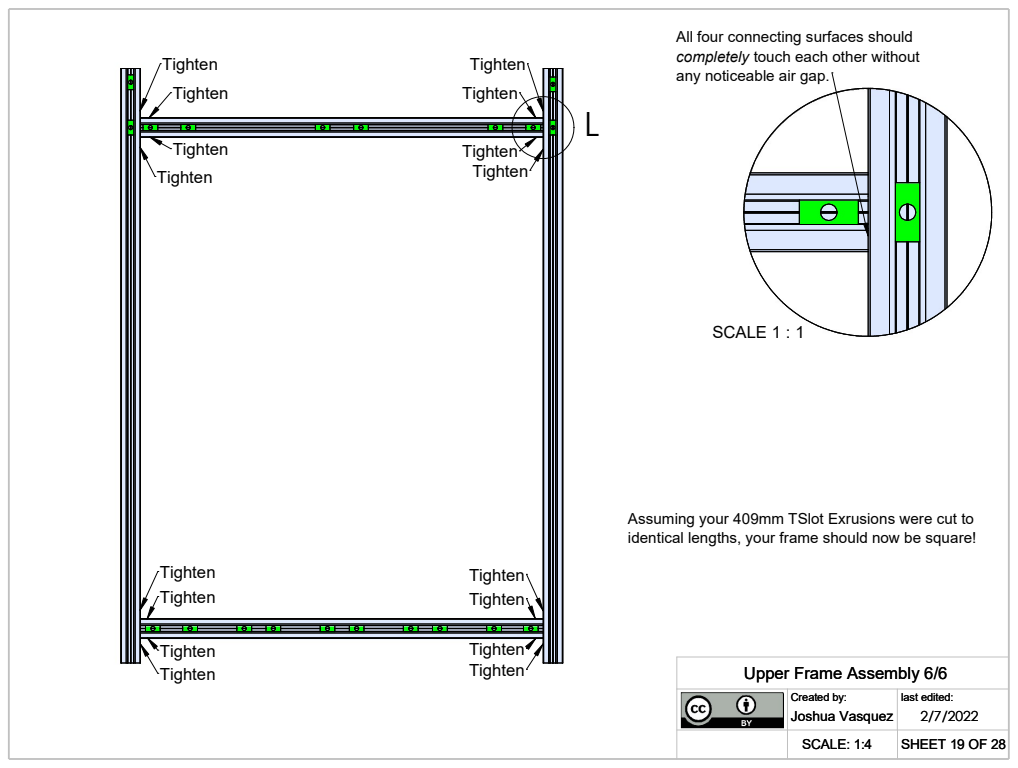
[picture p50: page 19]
SCALE 1 : 1; Tighten Tighten; Tighten

All four connecting surfaces should
completely touch each other without

any noticeable air gap. Tighten
Tighten

Assuming your 409mm TSlot Exrusions were cut to
identical lengths, your frame should now be square!

Upper Frame Assembly 6/6

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

SCALE: 1:4 | SHEET 19 OF 28

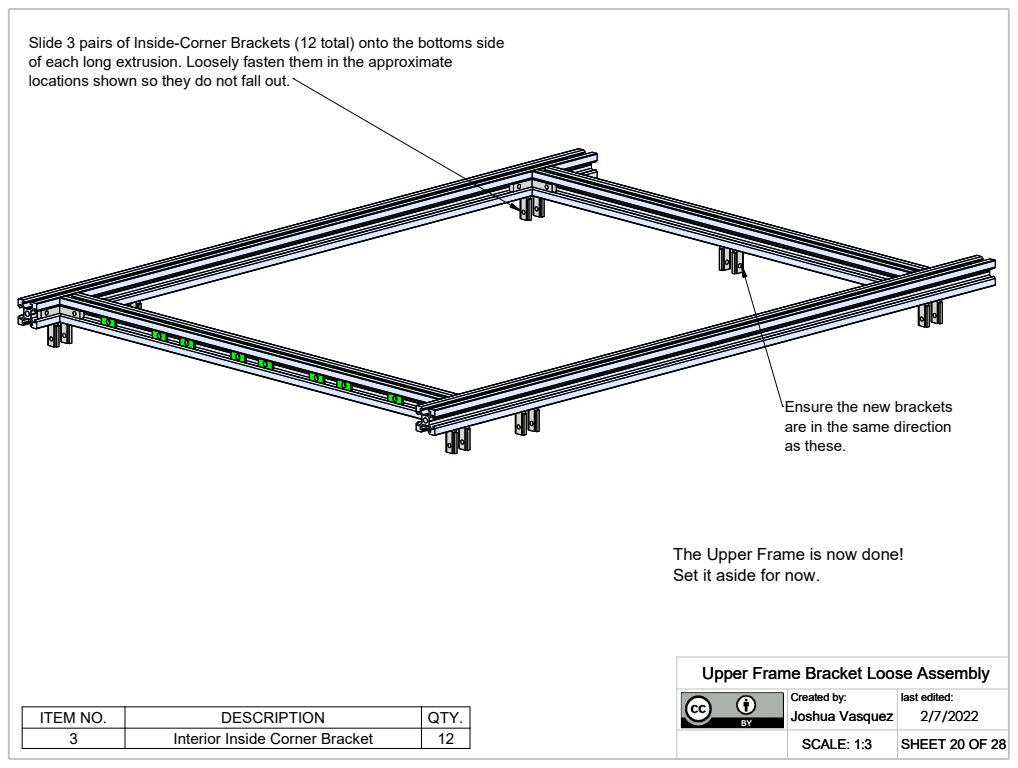
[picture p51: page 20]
SCALE: 1:3; SHEET 20 OF 28; Interior Inside Corner Bracket

Slide 3 pairs of Inside-Corner Brackets (12 total) onto the bottoms side
of each long extrusion. Loosely fasten them in the approximate
locations shown so they do not fall out.

Ensure the new brackets
are in the same direction
as these.

The Upper Frame is now done!
Set it aside for now.

Upper Frame Bracket Loose Assembly

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

ITEM NO. | DESCRIPTION | QTY.

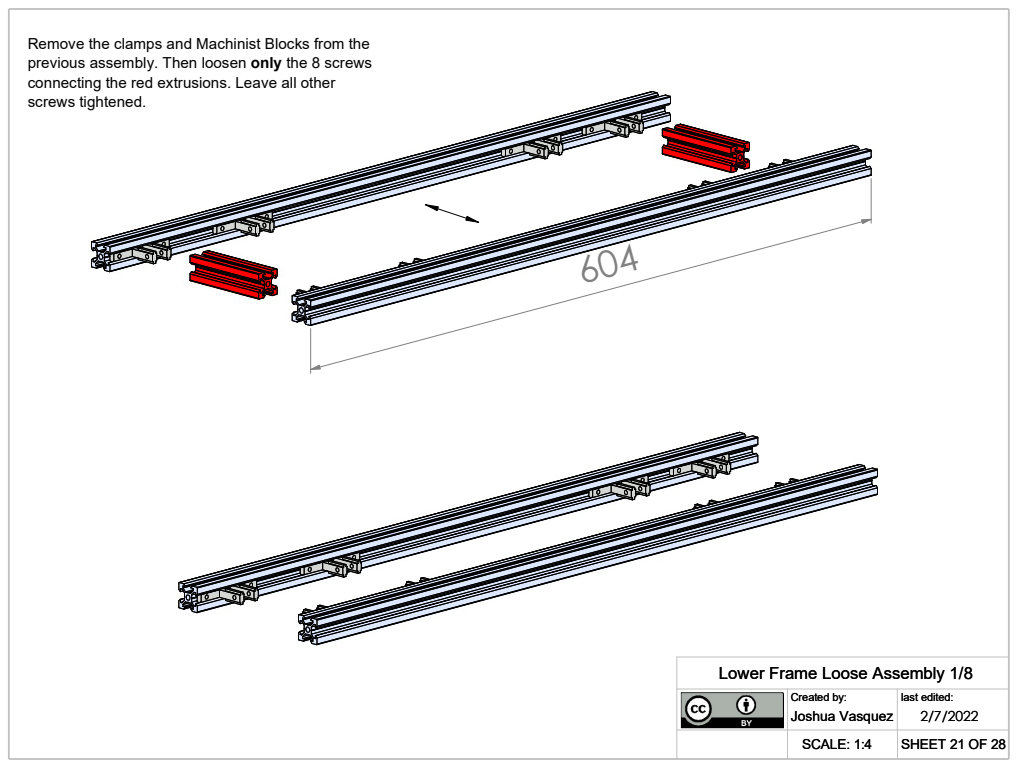
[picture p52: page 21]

Remove the clamps and Machinist Blocks from the
previous assembly. Then loosen only the 8 screws
connecting the red extrusions. Leave all other
screws tightened.

Lower Frame Loose Assembly 1/8

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

SCALE: 1:4 | SHEET 21 OF 28

On the left side slide in:
• 2 Stamped T Nuts on top
• 4 Stampted T Nuts on the bottom
Exact locations will be set later.

Assembled View Exploded View

Set these assemblies aside for now. On the right side slide in:
• 1 Stamped T Nut on top

Lower Frame Loose Assembly 2/8

ITEM NO. | DESCRIPTION | QTY.
3 | M5 Stamped Slide-In T Nut | 11
4 | T Nut Backing Spring | 11

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

SCALE: 1:4 | SHEET 22 OF 28

## Front Extrusion

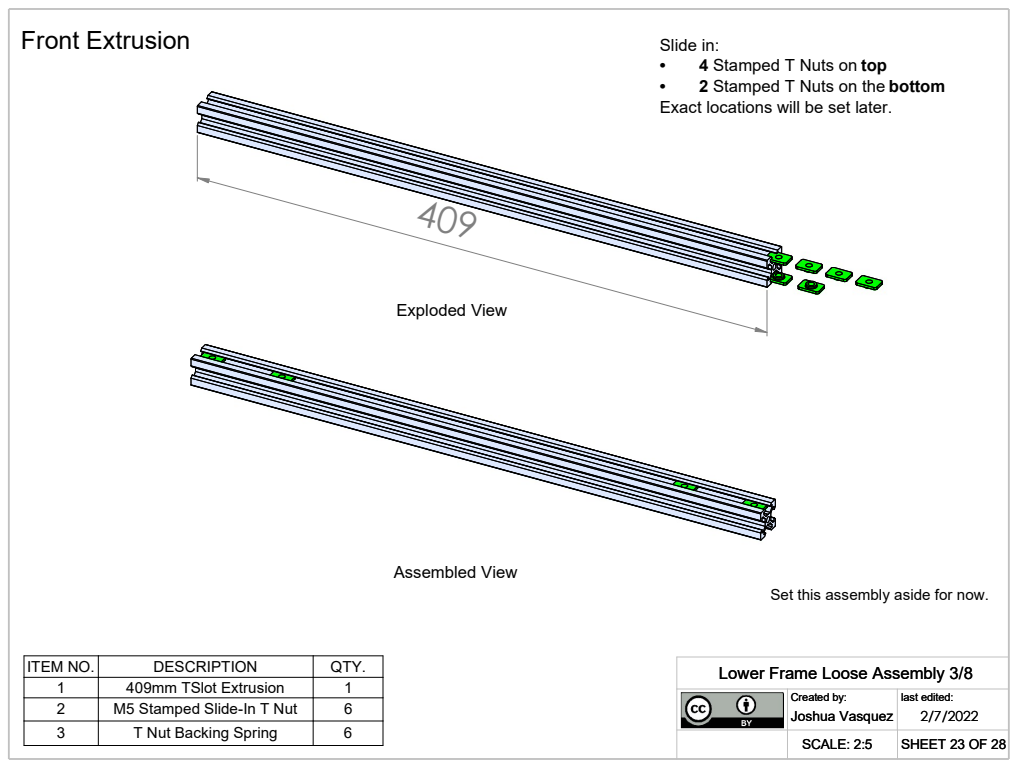
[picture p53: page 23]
Assembled View; Exploded View; ITEM NO.; DESCRIPTION; QTY.

Slide in:
• 4 Stamped T Nuts on top
• 2 Stamped T Nuts on the bottom
Exact locations will be set later.

Set this assembly aside for now.

Lower Frame Loose Assembly 3/8

1 | 409mm TSlot Extrusion | 1
2 | M5 Stamped Slide-In T Nut | 6
3 | T Nut Backing Spring | 6

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

SCALE: 2:5 | SHEET 23 OF 28

## Inner Front Extrusion

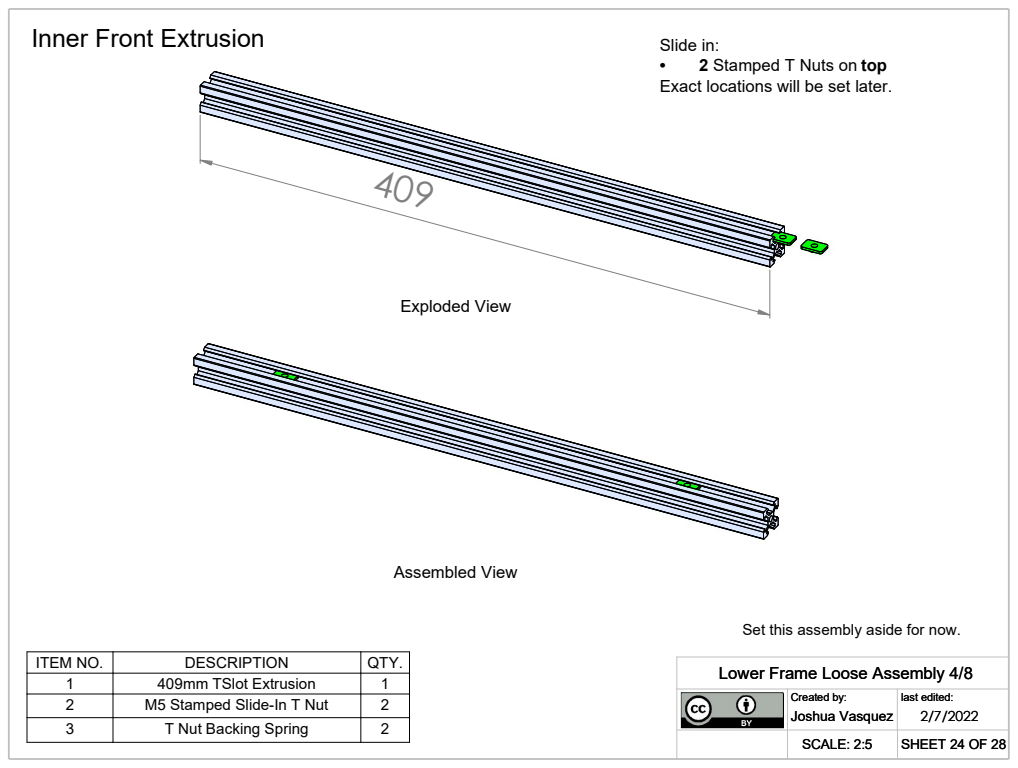
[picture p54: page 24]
Assembled View; Exploded View

Slide in:
• 2 Stamped T Nuts on top
Exact locations will be set later.

Set this assembly aside for now.

ITEM NO. | DESCRIPTION | QTY.
1 | 409mm TSlot Extrusion | 1
2 | M5 Stamped Slide-In T Nut | 2
3 | T Nut Backing Spring | 2

Lower Frame Loose Assembly 4/8

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

SCALE: 2:5 | SHEET 24 OF 28

## Inner Back Extrusion

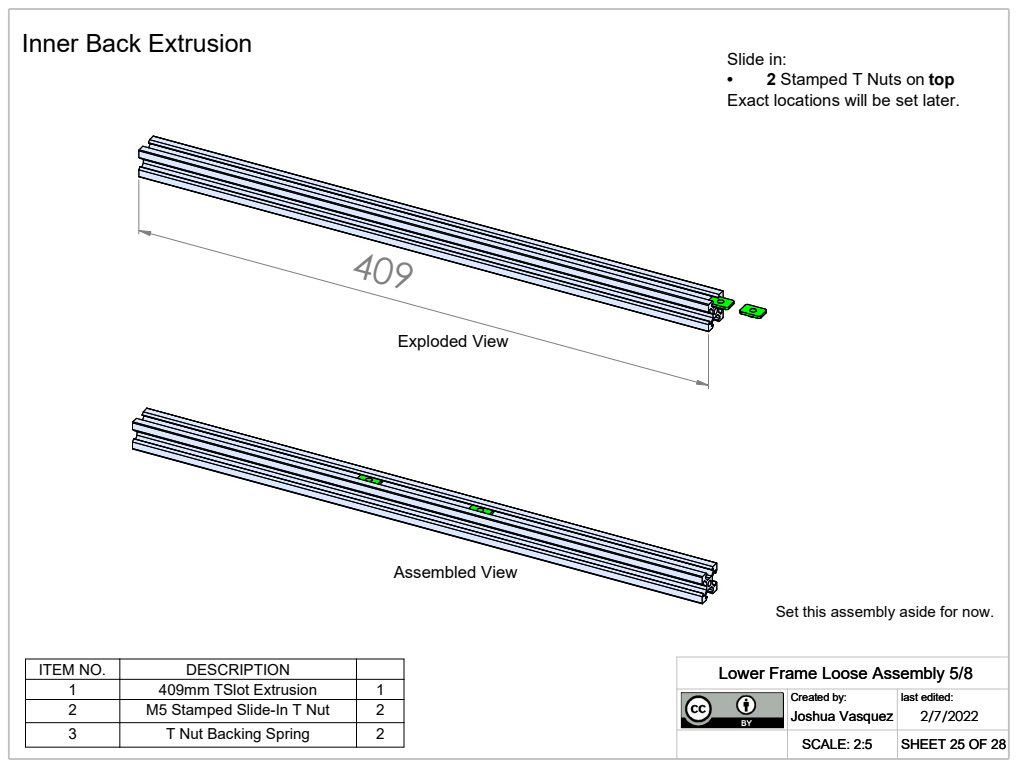
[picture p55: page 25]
Assembled View; Exploded View; ITEM NO.; DESCRIPTION

Slide in:
• 2 Stamped T Nuts on top
Exact locations will be set later.

Set this assembly aside for now.

Lower Frame Loose Assembly 5/8

1 | 409mm TSlot Extrusion | 1
2 | M5 Stamped Slide-In T Nut | 2
3 | T Nut Backing Spring | 2

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

SCALE: 2:5 | SHEET 25 OF 28

## Back Extrusion

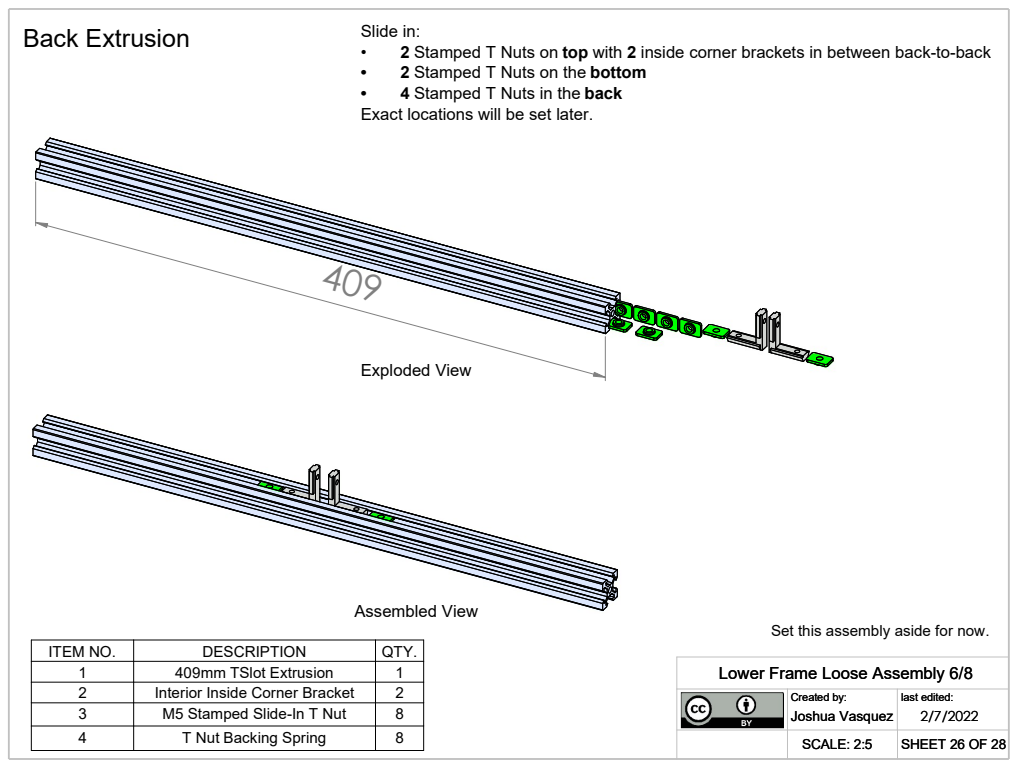
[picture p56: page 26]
Assembled View; Exploded View

Slide in:
• 2 Stamped T Nuts on top with 2 inside corner brackets in between back-to-back
• 2 Stamped T Nuts on the bottom
• 4 Stamped T Nuts in the back
Exact locations will be set later.

Set this assembly aside for now.

ITEM NO. | DESCRIPTION | QTY.
1 | 409mm TSlot Extrusion | 1
2 | Interior Inside Corner Bracket | 2
3 | M5 Stamped Slide-In T Nut | 8
4 | T Nut Backing Spring | 8

Lower Frame Loose Assembly 6/8

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

SCALE: 2:5 | SHEET 26 OF 28

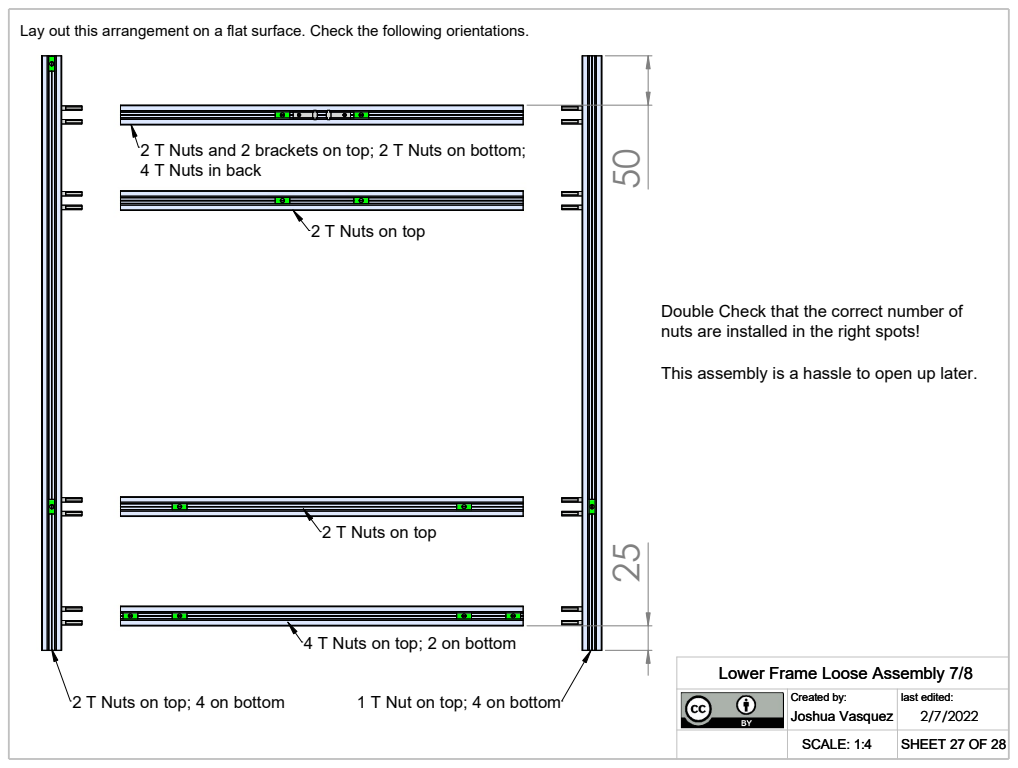
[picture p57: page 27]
2 T Nuts on top

Lay out this arrangement on a flat surface. Check the following orientations.

2 T Nuts and 2 brackets on top; 2 T Nuts on bottom;
4 T Nuts in back

2 T Nuts on top

Double Check that the correct number of
nuts are installed in the right spots!

This assembly is a hassle to open up later.

4 T Nuts on top; 2 on bottom

Lower Frame Loose Assembly 7/8

2 T Nuts on top; 4 on bottom

1 T Nut on top; 4 on bottom

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

SCALE: 1:4 | SHEET 27 OF 28

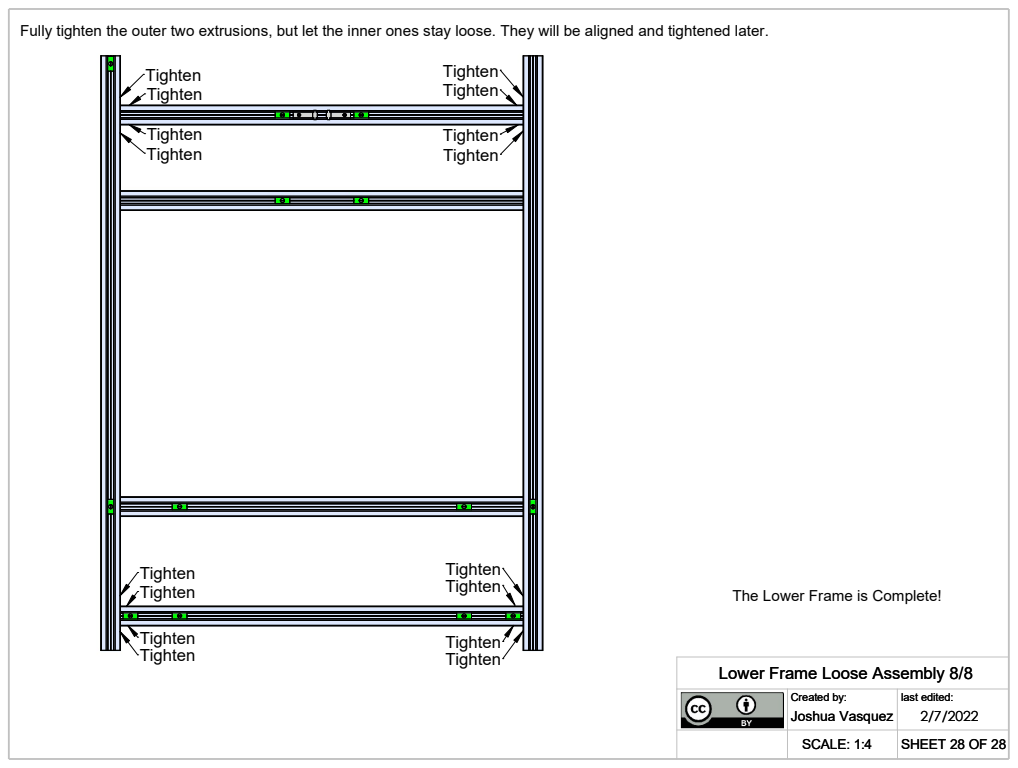
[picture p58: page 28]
Tighten Tighten; Tighten

Fully tighten the outer two extrusions, but let the inner ones stay loose. They will be aligned and tightened later.

The Lower Frame is Complete!

Lower Frame Loose Assembly 8/8

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

SCALE: 1:4 | SHEET 28 OF 28

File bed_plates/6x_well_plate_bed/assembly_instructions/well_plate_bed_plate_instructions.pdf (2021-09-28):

SHEET 1 OF 14; SCALE: 1:2; Joshua Vasquez; Created by:; last edited:

Well Plate Bed Plate Instructions

12 x | 3.20 | 8.73
6.30 X 90.00°


With a 90-deg Countersink tool,
countersink the following 12 holes
for an M3 flathead screw.

Note the orientation of each plate
using these slots as an identifying
feature.

ITEM NO. | DESCRIPTION | QTY.
1 | Top Layer Lower Plate | 1
2 | Top Layer Upper Plate | 1

Top Plate Pre-Processing

Created by: Joshua Vasquez | last edited: 9/28/2021

Only countersink the holes indicated! Double check the Orientation!

SCALE: 1:3 | SHEET 2 OF 14

### 26 x 3.20 THRU ALL 6.30 X 90.00°

SCALE: 1:3; SHEET 3 OF 14; Joshua Vasquez; Created by:; last edited:

With a 90-deg Countersink tool,
countersink the following 26 holes
for an M3 flathead screw.

Note the orientation of each plate
using these slots as an identifying
feature.

ITEM NO. | DESCRIPTION | QTY.
1 | Top Layer Lower Plate | 1
2 | Top Layer Upper Plate | 1

Bottom Plate Pre-Processing

Only countersink the holes indicated! Double check the Orientation!

SCALE: 3:4; SHEET 4 OF 14; Joshua Vasquez; Created by:; last edited:; Lower Plate Inserts ITEM NO.; DESCRIPTION; QTY.; Top Layer Lower Plate; M3 Tapered Heat Set Insert

Install the following heat set inserts in the locations specified using
the
Plate Press Technique.

Note the insert orientation. The
smooth side will insert first.

Before installing the inserts, check the
orientation of the inserts relative to this
feature.

Inserts should be flush with the top
surface when installed.

SCALE: 3:4; SHEET 5 OF 14; Joshua Vasquez; Created by:; last edited:; ITEM NO.; DESCRIPTION; QTY.; Upper Plate Inserts; Top Layer Upper Plate; M3 Tapered Heat Set Insert

Like before, install the following inserts in the locations specified.
Warning: this piece is not a copy of the prior one. Check the holes in relationship to the small cutouts.

SCALE: 1:2; SHEET 6 OF 14; Joshua Vasquez; Created by:; last edited:

Loosely lay out each plate from the prior steps such that they are upside down
from their previous orientation.

Plates are oriented such that
inserts were installed from the
bottom.

Top Plate Layout

Center Layout

Lay these parts on top of the previous and ensure that the holes match.

They will be secured in future steps.

ITEM NO. | DESCRIPTION | QTY.
1 | Middle Layer Left Plate | 1
2 | Middle Layer Right Plate | 1
3 | Middle Layer Upper Plate | 1
4 | Middle Layer Lower Plate | 1
5 | Middle Layer Center Plate | 1

Created by: Joshua Vasquez | last edited: 9/28/2021

SCALE: 1:4 | SHEET 7 OF 14

SCALE: 1:3; SHEET 8 OF 14; Joshua Vasquez; Created by:; last edited:

ITEM NO. | DESCRIPTION | QTY.
1 | M3 Flathead Screw, 8mm long | 4
2 | Bottom Layer Upper Plate | 1
3 | Bottom Layer Lower Plate | 1

First Wave Screw Installation

Joshua Vasquez; Created by:; last edited:

Second Wave Screw Installation

ITEM NO. | DESCRIPTION | QTY.
10 | M3 Flathead Screw, 8mm long | 14

Joshua Vasquez; Created by:; last edited:

Final Wave Screw Installation

ITEM NO. | DESCRIPTION | QTY.
10 | M3 Flathead Screw, 8mm long | 8


Press-Fit each clip through the first two plates until it hard-stops at the top of the third plate.

Note that theseclips have small burrs in them that will bend when you push them in.

Use a hard metal surface or clamps to gently push the clips into position. Do not use a hammering force as the plastic plates can shatter.

Joshua Vasquez; Created by:; last edited:; First Clip Installation; ITEM NO.; DESCRIPTION; 5205 Keystone Battery Clips
Joshua Vasquez; Created by:; last edited:; Full Clip Installation ITEM NO.; DESCRIPTION; Base Plate Sandwich; 5205 Keystone Battery Clips

Joshua Vasquez; Created by:; last edited:

The flathead screws go on the
countersunk side of the plate.

ITEM NO. | DESCRIPTION | QTY.
1 | Bed Plate | 1
2 | 10mm steel balls with M4 threads | 3
3 | M4 Flathead screw, 10mm long | 3

Bed Plate Assembly

SCALE: 1:3; SHEET 14 OF 14; Joshua Vasquez; Created by:; last edited:; Final Installation; ITEM NO.; DESCRIPTION; M3 Flathead Screw, 16mm long; Bed Plate Attachment Clips; Base Plate Sandwich; Bed Plate Assembly

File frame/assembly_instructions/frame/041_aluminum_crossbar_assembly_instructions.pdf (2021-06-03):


041 Aluminum Crossbar Assembly

Created by: Created by: Joshua Vasquez Joshua Vasquez | last edited: last edited: 6/3/2021 6/3/2021

SCALE: 1:2 | SHEET 1 OF 8

5

3

This Side is short.; This Side is long.

Note: This assembly step is for the generic brand pulleys only. If you are using genuine Gates brand pulleys, skip this page and see the next page.

Note that these have a noticeably smaller diameter than the
10mm outer-diameter versions.

ITEM NO. | DESCRIPTION | QTY
1 | M3 Standoff, 20mm long, 6mm wide | 1
2 | M4 Shoulder Screw, 25mm long | 2
3 | 20T toothless idler, 5mm bore | 1
4 | 20T Idler pulley, 2GT, 5mm bore | 1
5 | M5 Shim, 0.2mm thick, 7mm OD | 2
6 | Printed Pulley Spacer | 2
7 | Left Crossbar Pulley Reinforcement Plate | 1
8 | M3 Buttonhead Screw, 8mm long | 1

Note the orientation of the Reinforcement Plate

This Side is short.

Left Crossbar Generic Pulley Assembly

Created by: Joshua Vasquez | last edited: 6/3/2021

This Side is long.

SCALE: 1:1 | SHEET 2 OF 8

3

This Side is short.; This Side is long.

Note: This assembly step is for the genuine Gates brand pulleys only. If you are using generic brand pulleys, skip this page.

ITEM NO. | DESCRIPTION | QTY.
1 | M3 Standoff, 20mm long, 6mm wide | 1
2 | M4 Shoulder Screw, 25mm long | 2
3 | M5 Shim, 0.2mm thick, 7mm OD | 2
4 | Printed Pulley Spacer | 2
5 | Left Crossbar Pulley Reinforcement Plate | 1
6 | M3 Buttonhead Screw, 8mm long | 1
7 | 20T Idler pulley, 2GT, 5mm bore | 1
8 | 20T Toothless Idler pulley, 2GT, 5mm bore | 1

Note the orientation of the Reinforcement Plate

This Side is short.

Left Crossbar Gates Pulley Assembly

Created by: Joshua Vasquez | last edited: 6/3/2021

This Side is long.

SCALE: 1:1 | SHEET 3 OF 8

Left Crossbar Pulley Installation ITEM NO.; DESCRIPTION; QTY.

Install the pulley assembly upside-down (as
shown in the current view) such that this shim
doesn't fall out. Fully tighten all fastening points.

Left Crossbar Pulley Installation

1 | Pocketed Crossbar | 1
2 | Left Crossbar Pulley Assembly | 1
3 | M3 Buttonhead Screw, 10mm long | 1

Created by: Created by: Joshua Vasquez Joshua Vasquez | last edited: last edited: 6/3/2021 6/3/2021

SCALE: 1:3 | SHEET 4 OF 8

1

5

This side is long.; This Side is short.

Note: This assembly step is for the generic brand pulleys only. If you are using genuine Gates brand pulleys, skip this page and see the next page.

ITEM NO. | DESCRIPTION
1 | Crossbar X Limit Trigger | 1
2 | M3 10mm standoff, 4.5mm wide | 1
3 | M4 Shoulder Screw, 25mm long | 2
4 | M5 Shim, 0.2mm thick, 7mm OD | 2
5 | 20T Idler pulley, 2GT, 5mm bore | 1
6 | 20T toothless idler, 5mm bore | 1
7 | Printed Pulley Spacer | 1
8 | Right Crossbar Pulley Reinforcement Plate | 1
9 | M3 Buttonhead Screw, 8mm long | 1

Note the orientation of the Reinforcement Plate

This Side is short.

Right Crossbar Generic Pulley Assembly

Created by: Joshua Vasquez | last edited: 6/3/2021

This Side is long.

SCALE: 1:1 | SHEET 5 OF 8

1
4

This side is long.; This Side is short.

Note: This assembly step is for the genuine Gates brand pulleys only. If you are using generic brand pulleys, skip this page.

ITEM NO. | DESCRIPTION
1 | Crossbar X Limit Trigger | 1
2 | M3 10mm standoff, 4.5mm wide | 1
3 | M4 Shoulder Screw, 25mm long | 2
4 | M5 Shim, 0.2mm thick, 7mm OD | 2
5 | 20T Idler pulley, 2GT, 5mm bore | 1
6 | 20T toothless idler, 5mm bore | 1
7 | Printed Pulley Spacer | 1
8 | Right Crossbar Pulley Reinforcement Plate | 1
9 | M3 Buttonhead Screw, 8mm long | 1

Note the orientation of the Reinforcement Plate

This Side is short.

Right Crossbar Gates Pulley Assembly

Created by: Joshua Vasquez | last edited: 6/3/2021

This Side is long.

SCALE: 1:1 | SHEET 6 OF 8


Install the pulley assembly upside-down (as shown in the current view)
such that this shim doesn't fall out. Fully tighten all fastening points.

ITEM NO. | DESCRIPTION | QTY.
1 | Crossbar Assembly | 1
2 | M3 Buttonhead Screw, 20mm long | 1
4 | Right Crossbar Pulley Assembly | 1
5 | M3 Locknut | 1

Right Crossbar Pulley Installation

Created by: Created by: Joshua Vasquez Joshua Vasquez | last edited: last edited: 6/3/2021 6/3/2021

SCALE: 1:3 | SHEET 7 OF 8

Rail Installation; Exploded View; ITEM NO.; DESCRIPTION; QTY.; Crossbar with Pulley Assembly; M3 Buttonhead Screw, 10mm long; 395 or 400mm long MGN12 rail with MGN12C Carriage; M3 Locknut; X Axis Hard Stop; M3 Buttonhead Screw, 16mm long; Assembled View; This one is longer!

Loosely install the rail with the screws and lock nuts such
that the rail is snug but can slide around inside the holes
from the screw clearances by hand. It will be tightened later.

Created by: Joshua Vasquez | last edited: 6/3/2021

SCALE: 1:2 | SHEET 8 OF 8

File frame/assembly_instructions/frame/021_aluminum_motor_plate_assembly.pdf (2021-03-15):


Machined Motor Plate Assembly Instructions
Machined Motor Plate Assembly

Instructions Created by: Created by: Joshua Vasquez Joshua Vasquez | last edited: last edited: 3/15/2021 3/15/2021

SCALE: 1:1 | SHEET 1 OF 11

SCALE: 1:1; SHEET 2 OF 11; Spacer Assembly; Exploded Views; Assembled Views; Tall Motor Spacer with Insert; M3 Buttonhead Screw, 8mm long

solder in wires first!

On each set screw, just install the screw until it is flush with the inside surface.
If there is residual 3D printed gunk from the heat-set installation process, you
can clear it by installing the screw backwards first.

ITEM NO. | DESCRIPTION | QTY.
1 | Short Motor Spacer with Insert | 1

3 | Y Axis Limit Switch with Harness | 1
4 | M4 Set Screw, 25mm long | 2

Created by: Joshua Vasquez | last edited: 3/15/2021

SCALE: 1:1; SHEET 3 OF 11; Joshua Vasquez; Created by:; last edited:; Sheet1; ITEM NO.; DESCRIPTION; QTY.; 16-T 2GT Drive Pulley for 6mm belt; Nema17 XY Stepper: LDO-42STH60-2004MAC or 17HM19-2004S

Make two identical assemblies.

The vertical pulley spacing can be dialed in exactly later. ¹.3

Secure both included set screws onto the shaft, ensuring
that one set screw engages the flat part of the shaft.


ITEM NO. | DESCRIPTION
1 | M3 Standoff, 14mm long, 6mm wide | 2
2 | M3 Buttonhead Screw, 10mm long | 2
3 | Machined Left Motor Corner Bracket | 1

Left Motor Plate Assembly 1/4

Created by: Joshua Vasquez | last edited: 3/15/2021

SCALE: 1:1 | SHEET 4 OF 11


This part will be loose until the whole
assembly is mounted into the frame.

DESCRIPTION | | Left Motor Plate Assembly 2/4 ITEM NO.
4 | M5 Buttonhead Screw, 20mm long | 4
5 | Left Motor Spacer | 1

Created by: Joshua Vasquez | last edited: 3/15/2021

SCALE: 1:1 | SHEET 5 OF 11


These pulleys can be either Gates brand or Generic 2GT,
provided that they are between 8.5 and 10mm tall.

ITEM NO. | DESCRIPTION | QTY
5 | OpenBuilds M5 3mm Spacer | 2
6 | M5 Shim, 0.2mm thick, 7mm OD | 2
7 | pulley reinforcement plate for motor | 1
8 | M4 Shoulder Screw, 16mm-l, 5mm-d | 2
9 | M3 Buttonhead Screw, 6mm long | 2
10 | 20T toothless idler, 5mm bore | 1
11 | 20T Idler pulley, 2GT, 5mm bore | 1

Left Motor Plate Assembly 3/4

Created by: Joshua Vasquez | last edited: 3/15/2021

SCALE: 1:1 | SHEET 6 OF 11

Left Motor Plate Assembly 4/4 ITEM NO.; DESCRIPTION

2 | M3 Buttonhead Screw, 10mm long | 4
10 | M3 Washer | 4
11 | Stepper Motor with Drive Pulley | 1

Created by: Joshua Vasquez | last edited: 3/15/2021

SCALE: 1:1 | SHEET 7 OF 11


DESCRIPTION | | Right Motor Plate Assembly 1/4 ITEM NO.
1 | Machined Right Motor Corner Bracket | 1
2 | M3 Standoff, 14mm long, 6mm wide | 2
3 | M3 Buttonhead Screw, 10mm long | 2

Created by: Joshua Vasquez | last edited: 3/15/2021

SCALE: 1:1 | SHEET 8 OF 11


ITEM NO. | DESCRIPTION
3 | Tall Motor Corner Plate Spacer Assembly | 1
4 | M5 Buttonhead Screw, 30mm long | 4

This part will be loose until the whole
assembly is mounted into the frame.

Right Motor Plate Assembly 2/4

Created by: Joshua Vasquez | last edited: 3/15/2021

SCALE: 1:1 | SHEET 9 OF 11


These pulleys can be either Gates brand or Generic 2GT,
provided that they are between 8.5 and 10mm tall.

ITEM NO. | DESCRIPTION
3 | 20T Idler pulley, 2GT, 5mm bore | 1
4 | 20T toothless idler, 5mm bore | 1
5 | pulley reinforcement plate for motor | 1
6 | M3 Buttonhead Screw, 6mm long | 2
7 | M4 Shoulder Screw, 16mm-l, 5mm-d | 2
8 | M5 Shim, 0.2mm thick, 7mm OD | 2
9 | OpenBuilds M5 3mm Spacer | 2

Right Motor Plate Assembly 3/4

Created by: Joshua Vasquez | last edited: 3/15/2021

SCALE: 1:1 | SHEET 10 OF 11

ITEM NO.; DESCRIPTION; QTY; Right Motor Plate Assembly 4/4; M3 Buttonhead Screw, 10mm long; Stepper Motor with Drive Pulley; M3 Washer

Created by: Joshua Vasquez | last edited: 3/15/2021

SCALE: 1:1 | SHEET 11 OF 11

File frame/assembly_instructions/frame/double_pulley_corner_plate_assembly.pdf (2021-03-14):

B B

2 1


Double Pulley Corner Plate Assembly

Created by: Joshua Vasquez | last edited: 3/14/2021

SCALE: 1:1 | SHEET 1 OF 7

B B

Top View; Exploded View; Assembled View; M5 Shim, 0.2mm thick, 7mm OD; shim; washer

NOTE: This assemby step is for generic brand pulleys only. If you are using genuine Gates brand pulleys, skip this page and see the next page.

The raised bumps on this piece
point towards the standoffs.

Note the plate orientation!

This side is short.

This side is long.

ITEM NO. | DESCRIPTION
1 | M3 Standoff, 20mm long, 6mm wide | 2
2 | M4 Shoulder Screw, 25mm long | 1
3 | M3 Buttonhead Screw, 8mm long | 2

Left Corner Generic Pulley Assembly

5 | 20T Idler pulley, 2GT, 5mm bore | 2
6 | M5 Washer, 0.8-1.2mm thick | 2
7 | Left Corner Pulley Reinforcement Plate | 1

Created by: Joshua Vasquez | last edited: 3/14/2021

SHEET 2 OF 7

B B

shim; Top View; Exploded View; Assembled View; M3 Buttonhead Screw, 8mm long

NOTE: This assemby step is for Gates brand pulleys only. If you are using generic brand pulleys, skip this page and see the previous page.

The raised bumps on this piece
point towards the standoffs.

Note the plate orientation!

This side is short.

This side is long.

ITEM NO. | DESCRIPTION | QTY.
1 | M3 Standoff, 20mm long, 6mm wide | 2
2 | M4 Shoulder Screw, 25mm long | 1

Left Corner Gates Pulley Assembly

4 | M5 Shim, 0.2mm thick, 7mm OD | 2
5 | 20T Idler pulley, 2GT, 5mm bore | 2
6 | Left Corner Pulley Reinforcement Plate | 1

Created by: Joshua Vasquez | last edited: 3/14/2021

SHEET 3 OF 7

B

B

Exploded View; Assembled View

Install the pulley assembly upside-down
such that this shim seats properly on the
shoulder screw while the entire assembly
is screwed in.

These screws will stay loose
until this assembly is
installed ont he frame.

ITEM NO. | DESCRIPTION
1 1 | Left Corner Plate with Insert Installed | 1 1
5 5 | M3 Buttonhead Screw, 10mm long | 2 2
6 6 | M5 Buttonhead Screw, 20mm long | 3 3
10 10 | Left Corner Pulley Reinforcement Plate | 1 1

Left Corner Pulley Plate Assembly

Created by: Joshua Vasquez | last edited: 3/14/2021

SHEET 4 OF 7

### Top View

B B

Shim; Exploded View; Washer; Assembled View

NOTE: This assemby step is for generic brand pulleys only. If you are using genuine Gates brand pulleys, skip this page and see the next page.

The raised bumps on this piece
point towards the standoffs.

This side is short.

This side is long.

Note the plate orientation! Also note that this
orientation is different from the prior pulley
assembly.

ITEM NO. | DESCRIPTION
1 | M3 Standoff, 20mm long, 6mm wide | 2
2 | M4 Shoulder Screw, 25mm long | 1
3 | 20T Idler pulley, 2GT, 5mm bore | 2
4 | M5 Shim, 0.2mm thick, 7mm OD | 4
5 | M3 Buttonhead Screw, 8mm long | 2
6 | M5 Washer, 0.8-1.2mm thick | 2
7 | Left Corner Pulley Reinforcement Plate | 1

Right Corner Generic Pulley Assembly

Created by: Joshua Vasquez | last edited: 3/14/2021

SHEET 5 OF 7

### Top View

B B

Assembled View; Exploded View; Shim; M5 Shim, 0.2mm thick, 7mm OD

NOTE: This assemby step is for Gates brand pulleys only. If you are using generic brand pulleys, skip this page and see the previous page.

The raised bumps on this piece
point towards the standoffs.

This side is short.

This side is long.

Note the plate orientation! Also note that this
orientation is different from the prior pulley
assembly.

ITEM NO. | DESCRIPTION | QTY.
1 | M3 Standoff, 20mm long, 6mm wide | 2
2 | M4 Shoulder Screw, 25mm long | 1

Right Corner Gates Pulley Assembly

4 | 20T Idler pulley, 2GT, 5mm bore | 2
5 | Left Corner Pulley Reinforcement Plate | 1
6 | M3 Buttonhead Screw, 8mm long | 2

Created by: Joshua Vasquez | last edited: 3/14/2021

SHEET 6 OF 7

B B

Assembled View; Exploded View

Install this assembly upside-down such
that the shim seats properly on the
shoulder screw as the entire assemlby is
screwed in.

These screws will stay loose
until this assembly is
installed ont he frame.

ITEM NO. | DESCRIPTION
1 | Right Corner Plate with Insert Installed | 1
3 | Right Corner Pulley Assembly | 1
5 | M3 Buttonhead Screw, 10mm long | 2
7 | M5 Buttonhead Screw, 20mm long | 3

Right Corner Pulley Plate Assembly

Created by: Joshua Vasquez | last edited: 3/14/2021

SHEET 7 OF 7

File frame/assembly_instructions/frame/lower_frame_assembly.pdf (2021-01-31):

B B


Lower Frame Assembly

Created by: Joshua Vasquez | last edited: 1/31/2021

SCALE: 1:3 | SHEET 1 OF 10

B B

ITEM NO.; DESCRIPTION; QTY.; Back Right Foot; M5 Buttonhead Screw, 10mm long; Back Left Foot; Front Right Foot; Front Left Foot; Lower Frame

Flip the Lower Frame Assembly Upside Down. Slide each foot's T Nuts under each foot and then tighten all screws.

Note that these inside-corner
brackets should face downwards.
It may be easier to do this step by
dangling this end over the edge of a
table.

Exploded Upside Down View

Flip the frame right-side up when finished.

Assembled Right-Side Up View

Corner Foot Installation

Created by: Joshua Vasquez | last edited: 1/31/2021

SCALE: 1:6 | SHEET 2 OF 10

B B

A A Assembled View; Exploded View; Make 3 Assemblies.

With one hand, compress the coupler
onto the motor shaft to remove any
space on the motor shaft. Securely
screw down the coupler in this
configuration.

These are a 3 piece set.
Orientation of each piece
does not matter.

ITEM NO. | DESCRIPTION | QTY.
1 | 5mm to 8mm flexible plumb coupler | 1
2 | Nema 17 Stepper Motor | 1
3 | Z Thrust Bearing Spacer | 1
4 | 5mm Oversize Thrust Bearing | 1

Z Motor Thrust Coupling Assembly

Created by: Joshua Vasquez | last edited: 1/31/2021

SCALE: 1:1 | SHEET 3 OF 10

B B

Exploded View; Assembled View

Apply a dab of threadlock to the tip of the four M3 screws before tightening them down securely.

ITEM NO. | DESCRIPTION | QTY.
1 | M3 Buttonhead Screw, 12mm long | 4
2 | Back Plate Plate Assembly | 1
3 | Z Motor Thrust Coupling Assembly | 1
4 | M3 Washer | 4

Wires should
stick out in this
direction.

Back Z Motor Plate Assembly

Created by: Joshua Vasquez | last edited: 1/31/2021

SCALE: 1:1.5 | SHEET 4 OF 10

B B

SCALE: 1:1.5; SHEET 5 OF 10; M3 Washer; Exploded View

Apply a dab of threadlock to the tip of the four M3 screws before tightening them down securely.

Optional: motor wires could
poke up and out from this
cavity.

Assembled Top View
Scale 1:2

Wires should
stick out in this
direction.

Assembled View
Front Left Z Plate Assembly

ITEM NO. | DESCRIPTION | QTY.
1 | M3 Buttonhead Screw, 12mm long | 4
3 | Z Motor Thrust Coupling Assembly | 1

Created by: Joshua Vasquez | last edited: 1/31/2021

B B

SCALE: 1:1.5; SHEET 6 OF 10; ITEM NO.; DESCRIPTION; QTY.; M3 Washer; Wires should; Exploded View; Assembled View

Apply a dab of threadlock to the four M3 screws before tightening them down securely.

Optional: motor wires could
poke up and out from this
cavity.

Assembled Top View
Scale 1:2

stick out in this
direction.

Front Right Z Plate Assembly

1 | M3 Buttonhead Screw, 12mm long | 4
3 | Z Motor Thrust Coupling Assembly | 1

Created by: Joshua Vasquez | last edited: 1/31/2021

B B

tighten.; Top View

Load the Z Motor Plates into the frame to set the spacing of the internal loose extrusions. Push these internal extrusions into the plates and fully
tighten the 8 inside corner brackets shown below.

ITEM NO. | DESCRIPTION
1 | Base Frame Assembly with Feet | 1
2 | Back Z Plate Assembly | 1
3 | Front Left Z Plate Assembly | 1
4 | Front Right Z Plate Assembly | 1

Internal Extrusion Alignment

Created by: Joshua Vasquez | last edited: 1/31/2021

SCALE: 1:4 | SHEET 7 OF 10

B B

SCALE: 1:4; SHEET 8 OF 10; Z Plate Locating; holes.; Interior Inside Corner Bracket; Top View

First slide 2 pairs of inside-corner brackets (4 total) into position between both front
coupler plates, but do not tighten them.

Then, slide all M5 T
Nuts into position such
that they are directly
below their respective

Finally, relocate the
front plates to the
correct position.

Note that the other two
corner brackets from
earlier will slide into this
cavity.

Created by: Joshua Vasquez | last edited: 1/31/2021

ITEM NO. | DESCRIPTION

B B

Z Plate Tightening; ITEM NO.; DESCRIPTION; QTY.; M5 Buttonhead Screw, 10mm long; tighten; Top View

Tighten all screws shown below.

Created by: Joshua Vasquez | last edited: 1/31/2021

SCALE: 1:3 | SHEET 9 OF 10

B B


Slide 4 pairs of Inside-Corner Brackets into
the approximate locations shown here.
Keep them loose for now.

The Lower Frame Assembly is complete!

Inside Corner Bracket Installation

Created by: Joshua Vasquez | last edited: 1/31/2021

ITEM NO. | DESCRIPTION
5 | Interior Inside Corner Bracket | 8

SCALE: 1:3 | SHEET 10 OF 10

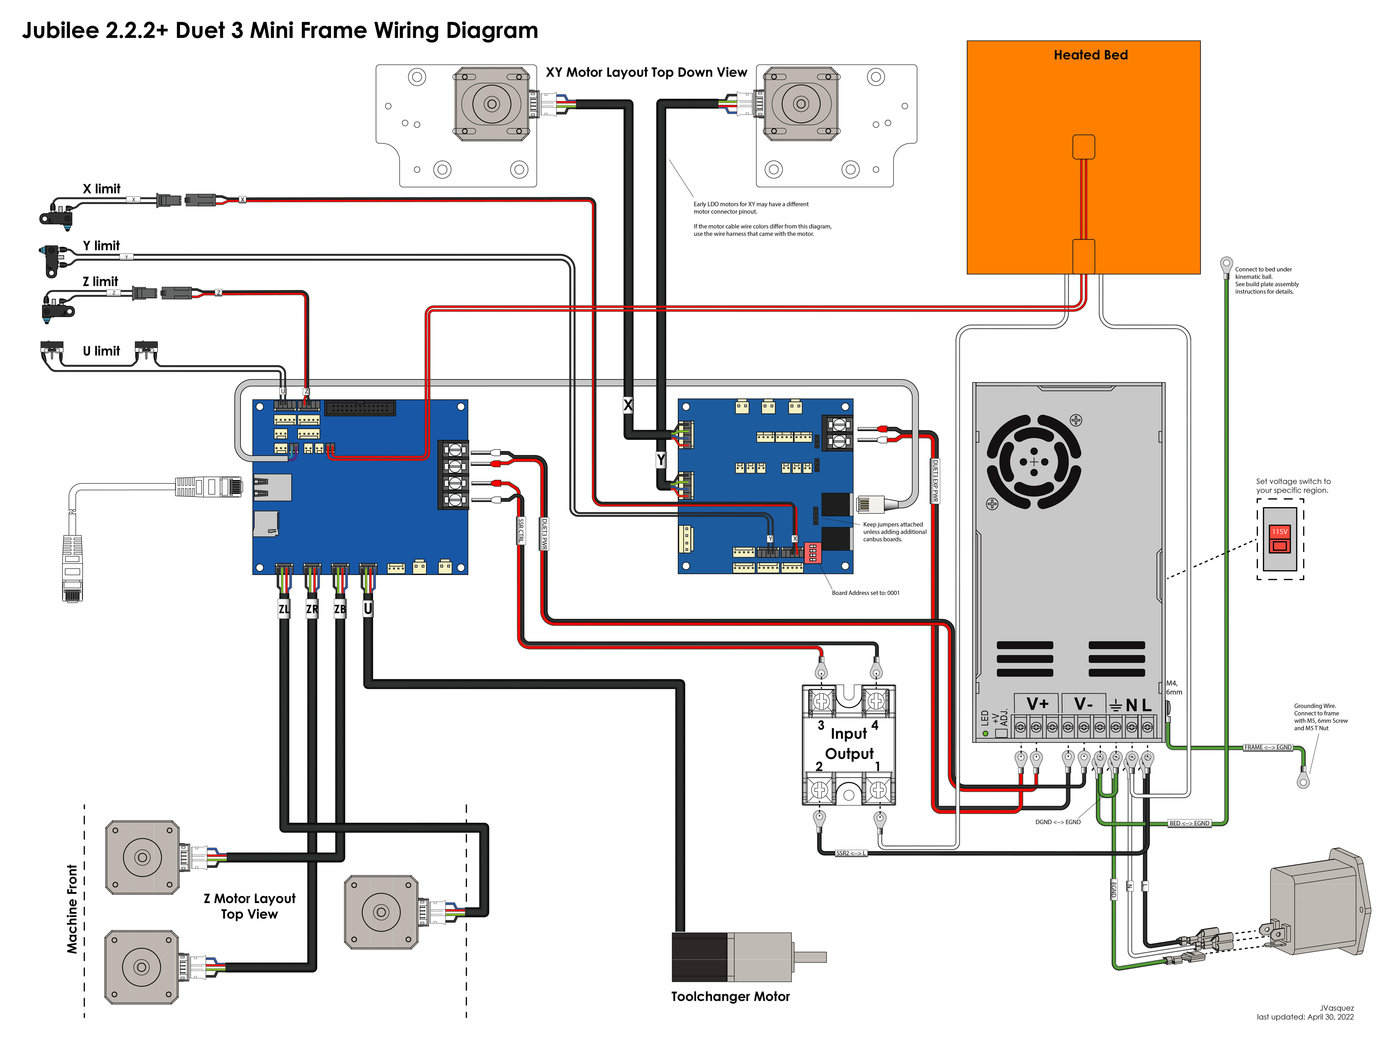
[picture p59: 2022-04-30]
frame/assembly_instructions/wiring/duet3_mini/duet3_mini_frame_wiring.png

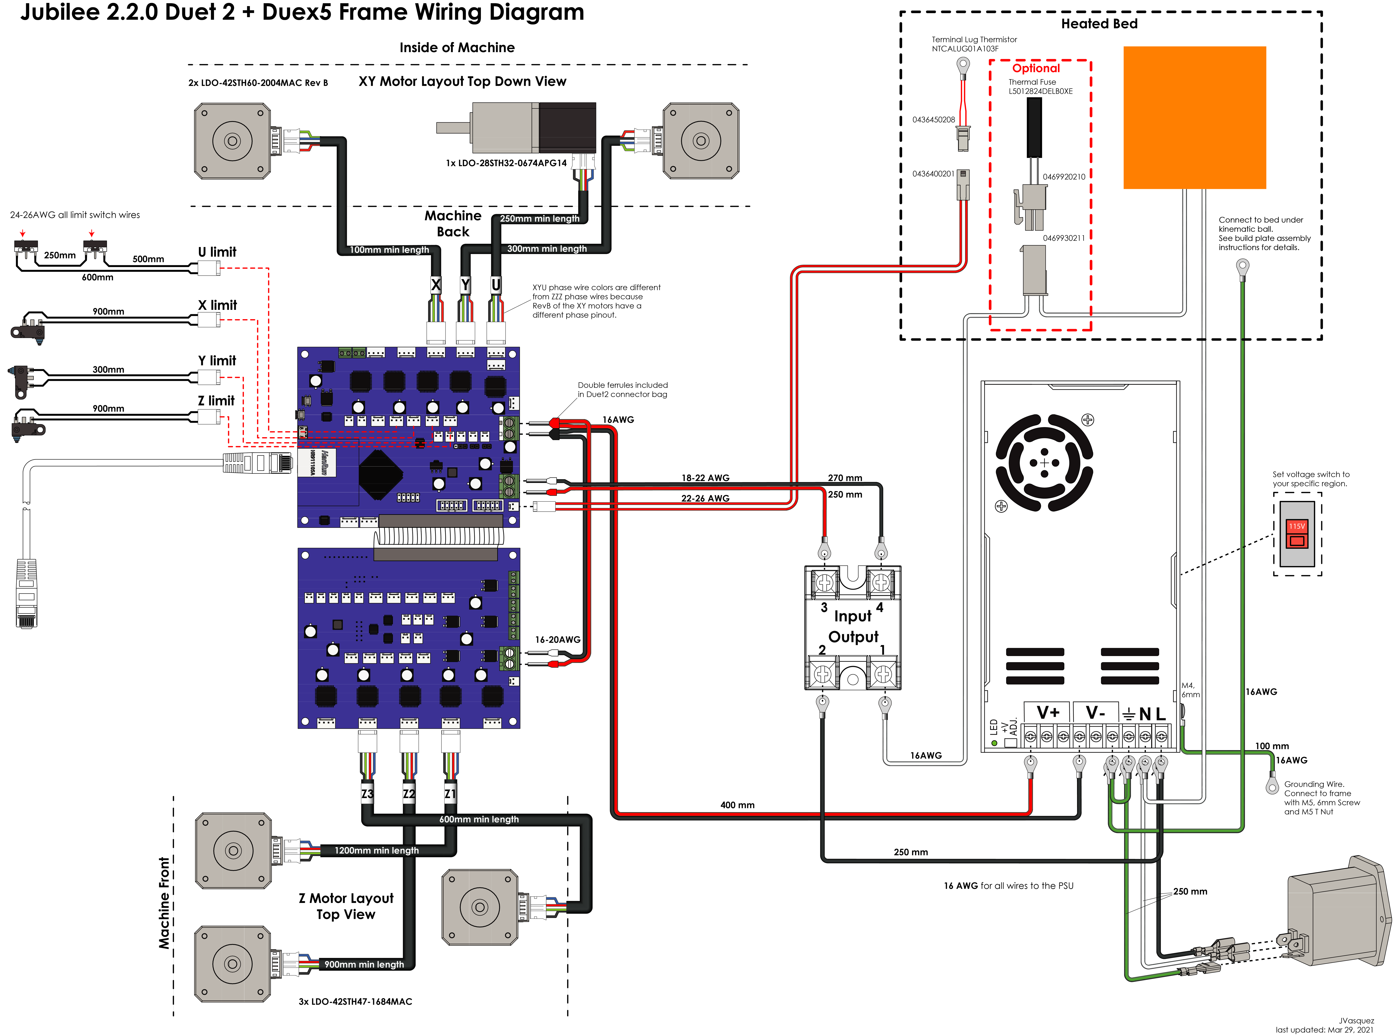
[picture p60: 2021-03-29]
frame/assembly_instructions/wiring/duet2/duet2_frame_wiring.png

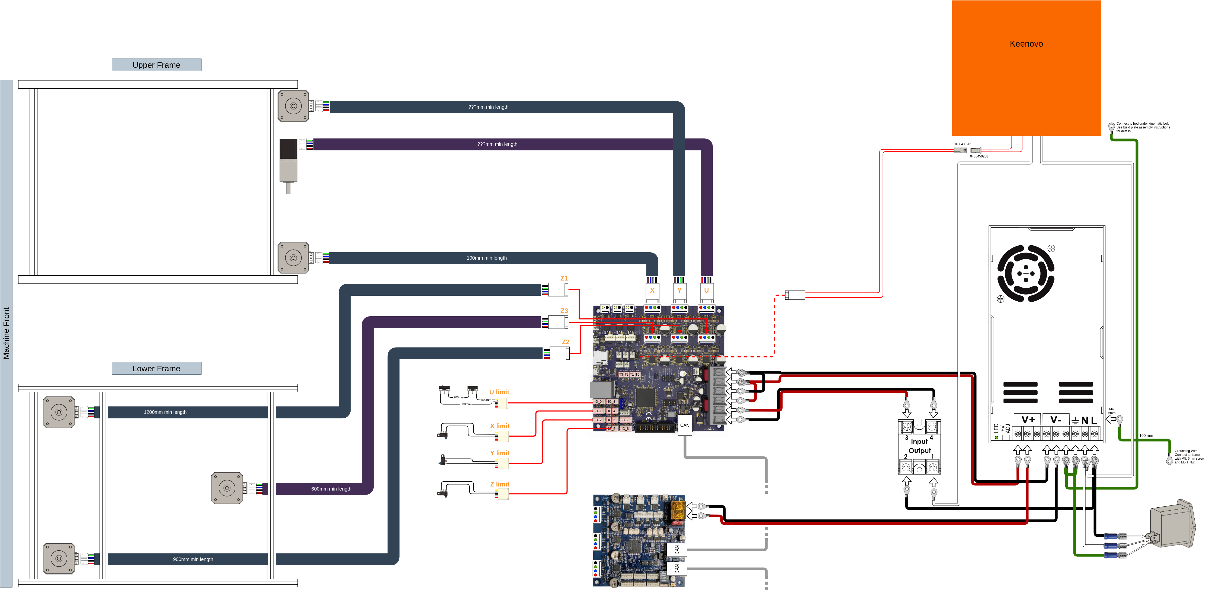
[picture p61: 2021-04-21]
frame/assembly_instructions/wiring/duet3/duet3_frame_wiring.png

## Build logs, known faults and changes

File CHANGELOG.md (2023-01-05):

# Changelog

All changes between releases are tracked here.

## rel/Jubilee 2.2.3 - In Progress
- Updated belt tuning frequency from 50 Hz to 61 Hz according to tests made by @Anima on Discord
  - Prints have noticeably less periodic ringing and ringing in corners.
- Instuctions updates
  - added notes about PSU internal fuses.
  - fixed ZL, ZR, ZB mixup in duet 3 wiring pdf.
- Improved Parking Post design to accommodate more extreme sizes
- Baby Bullet
  - Added Orbiter V2.0 clip for wire harnesses and updated instructions
  - Fan shrouds direct airflow lower (below the nozzle tip).
  - Added printed parts for mounting a Revo Micro
  - TODO: Updated Solidworks
  - TODO: Added STEP export of Orbiter 2.0 configuration.
- Added Duet3 Mini Config files
- Added Duet Panel Layout PDF to show back panel mounting locations
- Side Note: in a collaboration with Filastruder and Luke's Laboratory, [Jubilee Kits](https://www.filastruder.com/products/jubilee-motion-platform-kit?_pos=5&_sid=a2f60c0c4&_ss=r) for 2.2.2 entered the world on Feb 10, 2022
- Side Note: [Extruder Wire Harnesses](https://lukeslabonline.com/products/jubilee-tool-harness?_pos=1&_sid=1c51388a3&_ss=r) are now available through Luke's Laboratory
- TODO: Added Superslicer configuration
- TODO: add leveling feet

## rel/jubilee 2.2.2 - Oct 16, 2021
- Added a new default tool based on the Orbiter 1.5 Extruder, the "Baby Bullet"
  - both E3D "Groovemount" and threaded heatsinks are compatible for V6 and V7 style hotends
  - approx. 370 grams, about 80-100 grams lighter than the original default BMG Tool
  - features dual 5015 Blower Fans
  - includes step-by-step instructions for both groovemount and threaded types
  - additional provisioning info is in the [wiki](https://jubilee3d.com/index.php?title=Baby_Bullet_Extruder)
- Added M12 Threaded Heatsink Wrench
- Added custom bed plate for lab automation
  - holds up to 6 well plates of the common well plate size
  - can be fabricated from laser-cut, 3d printed, and off the shelf hardware
- Remodeled Adjustable Parking Post. Both dowel pin *height* and *width* are now adjustable parameters.
  - minimum dowel pin spacing can now be as thin as 35mm.
- Added new PSU Socket Holder (PSH2-02) for [Astrodyne 084.01001.00-RSI](https://www.mouser.com/ProductDetail/Astrodyne-TDI/0840100100-RSI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) Power Inlet Sockets. (These require 2x fuses.)
- Added Hard Stop on REL Base Plate to prevent the motor from twisting when locking tools.
- Added Tool Interface Diagram to show space constraints when designing custom tools.
- Added Diagrams for Duet 3 Mini Wire Harnesses with lengths and connectors
- Added preliminary SuperSlicer Config
  - Note that this config alters the machine jerk settings to produce good quality prints at high speeds.
- Added X-axis Limit Switch Hardstop
- Added Z-axis Hard Stops to prevent permanent machine damage in the case of a failed/misconfigured Z limit switch.
  - 3-point bed leveling needs to start very close to level now, but a broken Z limit switch will no longer warp the crossbar or bed plate. Note that the three Z-axis linear rails must be 400mm long. small adjustments need to be made to the assembly if the rails are actually 395mm (HIWIN).
- Moved the "Control Point" down to 2mm below the Z limit switch trigger position. (G31 in the config.) This change adds clearance to ensure that travel moves with not tools when z=0 do not shear the limit switch.
- T8x4 leadscrews are now the default in the BOM
- primary working branch renamed from *master* to *main*

### Changes to Printed Parts
- Updated Carriage Center Plate CCP-04 --> CCP-05
  - added space in the center
- Updated Carriage Back Plate CBP-05 --> CBP-06
  - made zip tie retention feature easier to print
  - added clearance for limit switch wires
- Updated REL Base Plate RLB-10 --> RLB-11
  - added a retention feature to prevent the motor from twisting.

### Shopping List Changes
- Fastener Sheet
  - +1 M3, 16mm screw (for the X-axis limit switch hardstop)
  - -1 M3, 10mm screw (swapped out for the 16mm one)
  - +2 M3 Heat Set Inserts
  - +2 M3 set screws, 10mm long
  - T8x4 Leadscrews changed to default. T8x2 Leadscrews changed to alternate.

## rel/jubilee 2.2.1 - Apr 21, 2021
- Updated Electronics Back Panel!
  - Back Panel supports hole patterns for (1) Duet 3 Mini + 3HC, (2) Duet 2 + Duex5, and (3) Duet 3 + 2 3HC's
  - Removed Tool Wiring Cable feedthrough holes. Tool wiring can be routed under the machine.
- Updated Default BMG Tool:
  - Flipped Wedge Plate Orientation in the Default BMG Tool. This orientation makes for a stiffer back plate.
  - Updated Default BMG Tool Fan Shroud to @edthesped's "Cappuccino" fan shroud. Uses 5015 fans instead of 4020 fans.
  - Added 2mm slot width to Cappuccino fan for extra vertical adjustment.
  - Added second Cappuccino fan model with wider slot for [Mechatronics 5015 fans](https://www.mechatronics.com/pdf/B5015.pdf)
  - Added pics to BMG Tool instructions from @msds. Fixes [#107](https://github.com/machineagency/jubilee/issues/107) and [#143](https://github.com/machineagency/jubilee/issues/143)
- Tool Template Updates:
  - Added Tool Wings to the Tool Template (2 variants in Solidworks, STEP, and STL)
  - Flipped Wedge Plate Orientation in the Tool Template Model. Preliminary tests show that this shape makes the tool plate much more resilient to creep.
- Merged [PR from Olby](https://github.com/machineagency/jubilee/pull/179) which updates the Duet3 Wiring Diagram to be in sync with the config files.
- The four M3 12mm screws on the front carriage have been swapped for the four M3 10mm screws on the back Z axis. Screw count did not change.

## rel/jubilee 2.2.0 - Dec 2, 2020
- More Permissive License!
  - Jubilee is licensed under Creative Commons 4.0 International License
  - Dropping the former "Share-Alike" restriction
- Massive Frame Assembly Instruction Overhaul
  - All M5 Drop-in T Nuts have been replaced with M5 Stamped Slide-in T Nuts. The former do not always seat properly into the extrusion when they are being installed.
  - Frame assembly instructions have been totally revamped to pre-load Slide-in T Nuts during assembly.
  - All M3 Slide-in T Nuts (used for connecting MGN12 rail to the 2020 extrusions) have been replaced with [Stamped M3 Slide In T-Nuts](https://www.aliexpress.com/item/32803077280.html) which are consistently better quality from Aliexpress
  - The process of squaring the outer frame makes better use of the Machinist Blocks, which means...
  - The 8x outer_frame_squaring_plate.STLs are no longer needed.
- Leadscrew Retainers are no longer needed. They have been removed from the assembly instructions.
  - As is, they were overconstraining the z axis screws.

### Config/Macro Changes
- Adding a RepRapFirmware 3+ Config Files for Duet2 + Duex5 boards
- Adding Safety and "tool-loaded" Checks to homing macros before executing a homing move. -- [contributed by @ProbiusSC](https://github.com/machineagency/jubilee/pull/133)
- bed.g
  - disabling mesh compensation at the beginning and re-enabling at the end. This is a precaution in case bed.g is called as a standalone macro. homez.g already disables mesh compensation before calling bed.g.

### Changes to Printed Parts
- [BZP-04](https://github.com/machineagency/jubilee/blob/master/frame/fabrication_exports/3d_printed_parts/frame/back_z_motor_plate.STL)
  - Added 1mm of height to where motor attaches to be consistent with the other two Z Motor Plates
- [LZP-04](https://github.com/machineagency/jubilee/blob/master/frame/fabrication_exports/3d_printed_parts/frame/front_left_z_motor_plate.STL)
  - Opened up M5 Screw Holes to 5.8mm to prevent collision of Slide-In TNut with Inside Corner Bracket 
- [RZP-04](https://github.com/machineagency/jubilee/blob/master/frame/fabrication_exports/3d_printed_parts/frame/front_right_z_motor_plate.STL)
  - Opened up M5 Screw Holes to 5.8mm to prevent collision of Slide-In TNut with Inside Corner Bracket 

### Shopping List Changes
- Fastener Sheet
  - All fasteners have been pulled into a separate tab.
  - All fasteners are now available as a single purchase from Filastruder
- M5 Stamped TNuts Introduced
  - These replace all M5 Drop-In TNuts
- Stamped TNut Backing Springs
- Keenovo Silicone Heated Pad Part Number Substitute
  - Replaced original Bed Heater with the one that includes a built-in 150C thermal cutoff for $3 more.
- Default BMG Extruder Shopping List
  - [Metal Tool Plates](https://shop.guildtek.com/index.php?main_page=product_info&cPath=1&products_id=4) available from Guildtek are now the default. These do not warp like the plastic ones do. Fixes [Issue #26](https://github.com/machineagency/jubilee/issues/26).

## rel/jubilee 2.1.2 - Sept 29, 2020
- Injection Molded Delrin Wedge Plates are now the standard for designing tool plates. Fixes [Issue #43](https://github.com/machineagency/jubilee/issues/43)
  - added injection molding specs sheet and STEP file with draft angles.
- Logo added to a [folder](https://github.com/machineagency/jubilee/tree/master/logo) in the main repository, courtesy of @troll on Discord
- Side and Back Panels for the frame are now available in HDPE from Filastruder. They are line items in the BOM.
- The Carriage Pulley now has an extra square nut to better resist plastic fatigue when screwed onto the Twist Lock.
- Added DXFs of Side and Back Panels to the [machineable parts folder](https://github.com/machineagency/jubilee/tree/master/frame/fabrication_exports/machined_parts/panels). These variants are router-friendly with the inclusion of Dogbone Fillets on inside corners for machining with up to a 3.175mm (1/8th in.) diameter endmill.
- Parking Post Part Number Corrected. The XX in PPBXX-04 and THXX-04 now reflect the dowel pin center-to-center distance.
  - PPB47-04 and TH47-04 regenerated, which are the correct parking post files for the pen tool.
  - PPB55-05 and TH55-05 created, which are the correct parking post files for the default extruder.
- Parking Post geometry updated for stiffness. It now uses a dovetail feature inspired by @Mr. Hobbit on Discord.
  - M3 8mm screws have been replaced with M3 10mm screws.
  - Instructions updated to reflect the new parking post geometry.
  
## Default Extruder Changes
- Replaced Delrin Compression Flexure with O-Rings. These are easier to source than a custom laser-cut Delrin part, but the old Delrin piece is still a viable option.
  - O-Rings should get a teeny bit of grease. (The same stuff as the leadscrews will work.)
- Tool Wings stick out an extra 5mm. The "pre-park" position has been backed off to 295mm in Y in the tool change macros to account for the extra distance. Overall build volume is unchanged.
  
### Config/Macro Changes
- config.g machine XY origin adjusted to reflect the documentation. (It was off by a couple mm.) Fixes [Issue #88](https://github.com/machineagency/jubilee/issues/88)
- XY Motor current has been increased to 2263mA. This is 80% of the peak current limit. (Note that LDO motor current limits are listed as *root mean square* not *peak* current values in the datasheet, so the *peak* current limit is 2829mA.)
- Tool Change Macros have been rewritten for more general use cases.
  - Tool Change Macros restore the Z height before pulling out the tool. This prevents tools from crashing into the bed when changing from a short to a tall tool.

### Changes to Printed Parts
- Carriage Pulley, [CPL-02](https://github.com/machineagency/jubilee/blob/master/frame/fabrication_exports/3d_printed_parts/toolchanger/toolchange_carriage/carriage_pulley.STL)

### Shopping List Changes
- Online Metals is now no longer a required supplier for frame components.
  - Side panel raw material has been replaced with three already-machined side panels from Filastruder.
- Carriage Pulley Assembly
  - -1 M3, 8mm set screw
  - +1 M3, 10mm set screw
  - +1 M3 Square Nut
- Default Extruder
  - +4 5mm ID, 9mm OD O-rings
- Parking Post
  - -2 M3, 8mm Buttonhead Screws
  - +2 M3, 10mm Buttonhead Screws
  
## rel/jubilee 2.1.1 - June 27, 2020

- REL Changes/Updates
  - Fixed Pulley tab is now slightly shorter to prevent rubbing on the back panel
  - Base Plate now accommodates a 3.0 or 3.2mm back panel
  - Base Plate motor distance to the back panel has been moved back 1mm for extra clearance for the Fixed Pulley tab.
  - Wire Rope Exit Holes are slightly wider on the base plate.
- Carriage Changes
  - Carriage Center Plate has four holes on the bottom to adjust the screws on the MGN12 Carriage without removing the front and back plates.
  - Wire Rope Exit Holes are slightly wider on SGC-02.
- Feet are now 46mm tall to accommodate heat sinks.
- Z-axis motors now use proper thrust bearings instead of two ring shims.
- Power Supply holder has one fewer fastener and more fastener hole clearance such that it can be screwed on with the socket installed

### Changes to Printed Parts
- [CCP-04](https://github.com/machineagency/jubilee/blob/master/frame/fabrication_exports/3d_printed_parts/toolchanger/toolchange_carriage/carriage_center_plate.STL)
- [z Thrust Bearing Spacer](https://github.com/machineagency/jubilee/blob/master/frame/fabrication_exports/3d_printed_parts/frame/z_thrust_bearing_spacer.STL)
- [SGC-02](https://github.com/machineagency/jubilee/blob/master/frame/fabrication_exports/3d_printed_parts/toolchanger/toolchange_carriage/spring_guide_capture.STL)
- [PSH-02](https://github.com/machineagency/jubilee/blob/master/frame/fabrication_exports/3d_printed_parts/frame/psu_socket_holder.STL)

- Taller Feet
  - [FLF-05](https://github.com/machineagency/jubilee/blob/master/frame/fabrication_exports/3d_printed_parts/frame/front_left_foot.STL)
  - [FRF-05](https://github.com/machineagency/jubilee/blob/master/frame/fabrication_exports/3d_printed_parts/frame/front_right_foot.STL)
  - [BLF-05](https://github.com/machineagency/jubilee/blob/master/frame/fabrication_exports/3d_printed_parts/frame/back_left_foot.STL)
  - [BRF-05](https://github.com/machineagency/jubilee/blob/master/frame/fabrication_exports/3d_printed_parts/frame/back_right_foot.STL)

- REL Parts
  - StepperOnline [Motor Clip](https://github.com/machineagency/jubilee/blob/master/frame/fabrication_exports/3d_printed_parts/toolchanger/toolchanger_locking_mechanism/stepper_online/lock_actuato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)
  - StepperOnline Base Plate [RLB-10S](https://github.com/machineagency/jubilee/blob/master/frame/fabrication_exports/3d_printed_parts/toolchanger/toolchanger_locking_mechanism/stepper_online/lock_actuato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)
  - LDO [Motor Clip](https://github.com/machineagency/jubilee/blob/master/frame/fabrication_exports/3d_printed_parts/toolchanger/toolchanger_locking_mechanism/lock_actuator_motor_clip.ST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)
  - LDO Base Plate [RLB-10](https://github.com/machineagency/jubilee/blob/master/frame/fabrication_exports/3d_printed_parts/toolchanger/toolchanger_locking_mechanism/lock_actuator_base_plate.ST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)
  - [Fixed Pulley](https://github.com/machineagency/jubilee/blob/master/frame/fabrication_exports/3d_printed_parts/toolchanger/toolchanger_locking_mechanism/fixed_half_pulley.STL)

### Shopping List Changes
- -1 M5 Drop-in T Nut
- -1 M5 8mm Buttonhead Screw
- +3 5.08mm ID thrust bearings for Z axis
- -6 M5, 10mm OD Shim

## rel/jubilee 2.1.0 - May 29, 2020 

- The toolchanger now uses either an LDO Motor or the original StepperOnline motor. You must print the motor clip and base plate pertaining to the motor you have.
- The Remote Elastic Lock now uses an actual spring instead of cut spring guide
    - 1000 were made in China and distributed to various Jubilee part resellers
- The frame now uses metal motor plates by default
    - These are both stiffer and serve as motor heatsinks
- The shopping list no longer features the embedded mag plate as the default and instead lists a plain plate with a high-temp magnetic sticky sheet.
- The bed plate has additional holes for:
    - a replaceable thermal fuse
	- a spring-steel cable chain
- The fan shroud screw holes for the Default Tool Plate have been lowered a couple mm.
- The Default Tool Plate has a small chamfer to improve printability (This change removes the effect of elephant's foot.)
- Added Frame Wiring Diagram and Default Extruder Tool Wiring Diagram
- Z-axis motors now have two stacked shims instead of one to reduce wear on the coupler
- Remote Elastic Lock redesign and compatible with both StepperOnline and LDO motor options
- Wiring Diagram
  - fixing toolchanger motor wiring color
  - changing Duex5 power wire gauge from 16 AWG to 16-20 AWG

### Changes to Printed Parts
- Printed Pulley Spacer can now be clipped in after-the-fact to ensure shims were installed correctly beforehand.
- Twist Lock Spacer outer diameter reduced for better printability across a range of printers
- Carriage Center Plate now has heat set inserts
- Z-axis motor plates
    - now have a chamfer on the bottom surface for better printability across a range of printers. (This change removes the effect of elephant's foot.)
	- Cutout for vertical extrusions has also been shrunk such that it can act as a locating feature.
    - offset added between the motor and the plate such that the leadscrews don't "bottom out" inside the coupler
- Z Motor Spacer height adjustment to accommodate for Z-axis motor plate change
- Feet are now 5mm taller to make space for optional heatsinks
- Added thumb handle to the Remote Elastic Lock

### Shopping List Changes
- +1 Subtle Design Mag Sheet
- +1 plain cast tool build plate
- -1 embedded magnet cast tool build plate
- +1 Motor Plate Set
- +4 M4 Shoulder Screw, 16mm long, 5mm diameter
- -4 M4 Shoulder Screw, 12mm long, 5mm diameter
- +12 M3 buttonhead screws, 12mm long; -12 M3 buttonhead screws, 10mm long 
- +1 Remote Elastic Lock Hub
- +1 Remote Elastic Lock Extension Spring
- +1 longer sleeve bearing, -1 old length sleeve bearing
- +1 M3 Set Screw, 5mm long for Remote Elastic Lock Hub
- +10 M3 Tapered Heat Set Inserts, 22 total
- -2 M5 Buttonhead Screw, 14mm long
- -0.0625in Delrin plate. No longer necessary with the new Remote Elastic Lock

### Updating from 2.0.2 to 2.1.0

#### Major Improvements
- double up Z Axis Shim.
- If your shim rings on the XY motion system had a 10mm outer diameter, swap them for shim rings with a 7 or 8mm outer diameter.

#### Negligible Improvements
- Replace Z Motor Plates and Z Motor Spacers.
- Replace Carriage Center Plate
- Replace Carriage Back Plate
- Replace Remote Elastic Lock. (Don't actually do this unless you haven't assembled it yet.)

## Hotfix to Jubilee 2.0.2 - May 18, 2020
If your are using printed corner plates, not the Delrin plates, and they do not fit with your pulley stackup, reprint these updated versions. This version is slightly more forgiving adding 0.2mm of tolerance in the Z dimension.
- LXR-03 [Left Crossbar Pulley Reinforcement Plate](https://github.com/machineagency/jubilee/blob/master/frame/fabrication_exports/3d_printed_parts/frame/left_crossbar_pulley_reinforcement_plate.STL) has a smaller diameter offset face to not interfere with the pulleys. Also: chamfer for easier shoulder screw insertion
- RXR-03 [Right Crossbar Pulley Reinforcement Plate](https://github.com/machineagency/jubilee/blob/master/frame/fabrication_exports/3d_printed_parts/frame/right_crossbar_pulley_reinforcement_plate.STL)  has a smaller diameter offset face to not interfere with the pulley. Also: chamfer for easier shoulder screw insertion
- LCR-03 [Left Corner Pulley Reinforcement Plate](https://github.com/machineagency/jubilee/blob/master/frame/fabrication_exports/3d_printed_parts/frame/left_corner_pulley_reinforcement_plate.STL) has a smaller diameter offset face to not interfere with the pulley. Also: chamfer for easier shoulder screw insertion
- RCR-03 [Right Corner Pulley Reinforcement Plate](https://github.com/machineagency/jubilee/blob/master/frame/fabrication_exports/3d_printed_parts/frame/right_corner_pulley_reinforcement_plate.STL) has a smaller diameter offset face to not interfere with the upper pulley. Also: chamfer for easier shoulder screw insertion

## Hotfix to Jubilee 2.0.2 - April 27, 2020
If your are using printed corner plates, not the Delrin plates, reprint them:
- LXR-02 [Left Crossbar Pulley Reinforcement Plate](https://github.com/machineagency/jubilee/blob/master/frame/fabrication_exports/3d_printed_parts/frame/left_crossbar_pulley_reinforcement_plate.STL) has a smaller diameter offset face to not interfere with the pulleys. Also: chamfer for easier shoulder screw insertion
- RXR-02 [Right Crossbar Pulley Reinforcement Plate](https://github.com/machineagency/jubilee/blob/master/frame/fabrication_exports/3d_printed_parts/frame/right_crossbar_pulley_reinforcement_plate.STL)  has a smaller diameter offset face to not interfere with the pulley. Also: chamfer for easier shoulder screw insertion
- LCR-02 [Left Corner Pulley Reinforcement Plate](https://github.com/machineagency/jubilee/blob/master/frame/fabrication_exports/3d_printed_parts/frame/left_corner_pulley_reinforcement_plate.STL) has a smaller diameter offset face to not interfere with the pulley. Also: chamfer for easier shoulder screw insertion
- RCR-02 [Right Corner Pulley Reinforcement Plate](https://github.com/machineagency/jubilee/blob/master/frame/fabrication_exports/3d_printed_parts/frame/right_corner_pulley_reinforcement_plate.STL) has a smaller diameter offset face to not interfere with the upper pulley. Also: chamfer for easier shoulder screw insertion

## rel/jubilee_2.0.2 - Apr 11, 2020

### Major Fixes/Updates from Jubilee 2.0.1
- The frame is now Gates Pulley Compatible.
    - Either Genuine Gates pulleys or generic pulleys can be dropped into the machine. Note that Gates Pulleys are slightly taller, so shims and washers have been called out in the instructions to handle the height differences. Several printed parts have been adjusted, and they are called out below.
- All Delrin Corner Plates are now 3D printed except the Cinch Plates. (You can still use the laser-cut ones, but you may need to add shim.)
    - This is to to handle intercompatibility with Gates/Generic pulleys. The Gates pulleys require taller shoulder screws, so I've opted for thickening these parts instead of adding shim.
- Metal Motor Plate Changes
    - Both Motor Plates now have a counterbore feature to accommodate the thicker motor spacer. This change was driven by the geometry changes to make the Gates pulleys a drop-in replacement.
- Printed Motor Plate changes
    - slot for the stepper motor is now 11.4mm in radius to accomodate coarse 3D printer tolerances. Fixes [issue #68](https://github.com/machineagency/jubilee/issues/68)
    - Printed Right Motor Plate now has a deeper counterbore feature
- CAD Model Changes
    - CAD model now displays the aluminum crossbar instead of the 6mm carbon fiber one. The carbon fiber crossbar is preserved as a reference in another configuration.
	- All M5 Low Profile screw models were replaced with buttonheads, which is what the shopping list specifies.
	- Solidworks Model Zip file has been replaced with all components in their original folder structure. No longer requires using Git-LFS, which had bandwidth limits.
	- Front Left and Front Right MGN12 Rails attach to the 2020 extrusion with 5 screw, not 4 screws, to be conisistent with the back Z rail. Fixes [Issue #72](https://github.com/machineagency/jubilee/issues/72)
- Z Axis Assembly Changes
    - Spacing between dowel pins is now consistent on all three bed couplers. Fixes [Issue #59](https://github.com/machineagency/jubilee/issues/59)
    - All three printed components that couple the bed to the frame have heat-set inserts
	- Bed springs now connect with a bent solder terminal lug
    - Spring Stock for the bed springs has been replaced with proper 15mm springs
    - Overall, adding springs to the bed is now much easier to assemble and remove.
- Carriage Changes
    - added a spacer inside the carriage center plate on the Twist Lock Assembly to remove axial force on the carriage pulley (performance improvement) Addresses [Issue #58](https://github.com/machineagency/jubilee/issues/58)
	- replaced M3 16mm Flathead screws with Buttonhead screws (reduces unique part count)
	- Twist lock has been bumped forward 0.2mm to improve compatibility with picking up E3D tool plates
	- Carriage Back Plate has a Zip Tie tab for better Z axis cable management
	- Carriage Center Plate now has enough space to accomodate a variant of the current limit switch (PN: D2HW-C202MR), which has flying leads.
- Default Tool/Extruder Changes
    - Wedge Plate Geometry has been bumped forward ~0.35mm to change twist lock "logking" position to be slightly less than 180 degrees.
	- Screw holes for the fan shround have been bumped down slightly.
- Electronics Back Panel Changes
    - M5 panel mounting screws have been scooched over a few mm to make space for installation with the XY motors installed
	- cutout has been added in the corner to make room for the 3D Printed PSU Socket
	- Pocket for Bed wires has been relocated upwards in prep for a cable chain on the bed
	- Bed SSR has been relocated upwards in prep for a cable chain on the bed
- 120v Side Panel Changes
    - PSU cutout has been removed and replaced with a printed part. This change makes the power inlet socket much easier to swap for alternates.
	- The four M5 Screw holes in the corner have been scooched in 5mm
- Ethernet Side Panel Changes
	- Four M5 Screw holes in the corner have been scooched in 5mm
- Updated instructions for
    - toolchanger carriage assembly
    - bed plate
	- double pulley corner plates
	- left and right motor corner plates (and upgrade)
	- Z axis assembly. New instructions for bent terminal lugs.
	- heat set insert list
	- default extruder. Fixes [Issue #70](https://github.com/machineagency/jubilee/issues/70)

### Shopping List Changes
- The 2.0.1 Y axis limit switch (Part Num: D2HW-BL201H) has been reverted to the original switch from 2.0 (Part Num: D2HW-C201H).
    - The original Right Motor Plate Spacer was too short to fully embed the Y axis switch, but resizing for the Gates pulley option added enough space to add the original switch in. Overall, reducing the unique part count makes the project easier to order and assemble.
- Shoulder Screws are now sourced from [Filastruder](https://www.filastruder.com/collections/railcore/products/shoulder-screws-bolts?variant=17989593104455), which is slightly cheaper than McMaster-Carr.
- All six 20mm long, 5mm diameter shoulder screws have been replaced with 25mm long versions.
- The three Bed Retension Springs are now a stock part from [Aliexpress](https://aliexpress.com/item/33043988987.html?spm=a2g0s.9042311.0.0.447133edZMsmcq). (Order the 15mm version.)
    - 2.0.1 (and before) had instructions for making your own springs out of spring stock. This was a TON of extra work for a part you can just buy.
- Bed Retension Clips are now a different type of Terminal Lug
    - The three Keystone [7328](https://www.digikey.com/product-detail/en/keystone-electronics/7328/36-7328-ND/316697) Terminal Lugs on the bed and the three M2 set screws have been replaced by six [4000](https://www.digikey.com/product-detail/en/keystone-electronics/4000/36-4000-ND/316071) Terminal Lugs, which are much easier to bend around the spring.
- three more M3 heat set inserts
- pack of washers for generic pulleys.
- The Belleville disc spring is no longer required and has been removed
- The four M3, 16mm Flathead screws on the Carriage Front Plate have been replaced with four M3 12mm long Buttonhead screws.
- Previous Power Inlet Socket from Amazon (ASIN: B07C184P7L) now has two alternates listed from Digikey (Part Num: CCM2178-ND‎) and Mouser (Part Num: 446-084.01001.00-RSI).
    - The alternates are twin fused to account for a short-to-ground failure mode in a Hot-Hot 220V configuration (rare, but possible in some countries). They are set to become the primary power inlet sockets in a future revision.

### Config File Changes
- In **config.g**, the machine's XY Origin has been adjusted to be relative to the carriage's ZProbe location when no tools are present. See the [Frame Layout](https://github.com/machineagency/jubilee/wiki/Frame-Layout) for diagrams.
    - *bed.g* has been adjusted to reflect the new "ZProbe-Centric" origin
    - **tfreeX.g**, **tpreX.g**, and **tpostX.g** have had their parking post locations adjusted to reflect the new "ZProbe-Centric" XY origin.
    - tools are now released 1m behind where they are picked up. This is such that they can be pushed in Y first to contact the tool balls before locking them. This is a workaround until we get nice slippy Delrin replacement plates.
    - **tool_lock.g** now includes a slight 0.5mm push forward while engaging the twist lock.

### Updating from 2.0.1 to 2.0.2
If you would like to have the future option of updating to genuine Gates pulleys, the following part **must** be reprinted
- 4x [Printed Pulley Spacer](https://github.com/machineagency/jubilee/blob/master/frame/fabrication_exports/3d_printed_parts/frame/printed_pulley_spacer.STL)
- RMS-05 [Right Motor Plate Spacer](https://github.com/machineagency/jubilee/blob/master/frame/fabrication_exports/3d_printed_parts/frame/right_motor_corner_bracket_spacer.STL)
- RMP-03 [Right Motor Plate](https://github.com/machineagency/jubilee/blob/master/frame/fabrication_exports/3d_printed_parts/frame/right_motor_plate.STL)
- CPB-03 [Carriage Back Plate](https://github.com/machineagency/jubilee/blob/master/frame/fabrication_exports/3d_printed_parts/toolchanger/toolchange_carriage/carriage_back_plate.STL)
- 2x [Belt Clasp](https://github.com/machineagency/jubilee/blob/master/frame/fabrication_exports/3d_printed_parts/frame/belt_clasp.STL)
- LXR-01 [Left Crossbar Pulley Reinforcement Plate](https://github.com/machineagency/jubilee/blob/master/frame/fabrication_exports/3d_printed_parts/frame/left_crossbar_pulley_reinforcement_plate.STL) (New!)
- RXR-01 [Right Crossbar Pulley Reinforcement Plate](https://github.com/machineagency/jubilee/blob/master/frame/fabrication_exports/3d_printed_parts/frame/right_crossbar_pulley_reinforcement_plate.STL) (New!)
- LCR-01 [Left Corner Pulley Reinforcement Plate](https://github.com/machineagency/jubilee/blob/master/frame/fabrication_exports/3d_printed_parts/frame/left_corner_pulley_reinforcement_plate.STL) (New!)
- RCR-01 [Right Corner Pulley Reinforcement Plate](https://github.com/machineagency/jubilee/blob/master/frame/fabrication_exports/3d_printed_parts/frame/right_corner_pulley_reinforcement_plate.STL) (New!)
- 2x LMR-01 [Motor Reinforcement Plate](https://github.com/machineagency/jubilee/blob/master/frame/fabrication_exports/3d_printed_parts/frame/motor_reinforcement_plate.STL) (New!)

The following parts were added/tweaked to better accomodate E3D tool plates
- TLS-01 [Twist Lock Spacer](https://github.com/machineagency/jubilee/blob/master/frame/fabrication_exports/3d_printed_parts/toolchanger/toolchange_carriage/twist_lock_spacer.STL) (New!)
- [Wedge Plate](https://github.com/machineagency/jubilee/blob/master/tools/jubilee_tools/tools/base_tool/fabrication_exports/wedge_plate.STL) 

The following parts were added/tweaked for ease of sourcing parts or assembly:
- FXP-09 [Fixed Half Pulley](https://github.com/machineagency/jubilee/blob/master/frame/fabrication_exports/3d_printed_parts/toolchanger/toolchanger_locking_mechanism/fixed_half_pulley.STL)
    - The hole for the 16mm long M3 screw is now slightly larger to make it easier to screw in.
- BBC-04 [Back Bed Coupler](https://github.com/machineagency/jubilee/blob/master/frame/fabrication_exports/3d_printed_parts/frame/back_bed_coupling_lift.STL)
    - has a threaded heat-set insert
- LBC-04 [Front Left Bed Coupler](https://github.com/machineagency/jubilee/blob/master/frame/fabrication_exports/3d_printed_parts/frame/front_left_bed_coupling_lift.STL)
    - has a threaded heat-set insert
- RBC-04 [Front Right Bed Coupler](https://github.com/machineagency/jubilee/blob/master/frame/fabrication_exports/3d_printed_parts/frame/front_right_bed_coupling_lift.STL)
    - has a threaded heat-set insert
- PSH-01 [PSU Socket Holder](https://github.com/machineagency/jubilee/blob/master/frame/fabrication_exports/3d_printed_parts/frame/psu_socket_holder.STL) (New!)
    - This part to replace the acrylic cutout, which was brittle and prone to cracking. It's also easier to modify a 3D printed part for slightly different sized PSU sockets. 
	
The following parts were tweaked for aesthetics:
- LMS-04 [Left Motor Plate Spacer](https://github.com/machineagency/jubilee/blob/master/frame/fabrication_exports/3d_printed_parts/frame/left_motor_corner_bracket_spacer.STL)

## rel/jubilee_2.0.1 - Mar 10, 2020

### Major Fixes/Updates from 2.0
- The [Aluminum Crossbar](https://www.mandalaroseworks.com/jubilee/crossbar) is now available from Mandala Rose Works for $80. It is now the default in the BOM. Should you choose to upgrade from the carbon fiber crossbar, you will need to:
    - Print the latest [Right Motor Plate Spacer](https://github.com/machineagency/jubilee/blob/master/frame/fabrication_exports/3d_printed_parts/frame/right_motor_corner_bracket_spacer.STL)
    - Print the [X Limit Trigger](https://github.com/machineagency/jubilee/blob/master/frame/upgrades/aluminum_crossbar/fabrication_exports/stls/x_limit_trigger.STL)
    - purchase 1x M3, 10mm standoff from [McMaster-Carr](https://www.mcmaster.com/95947a006)
    - purchase 1x M3, 16mm buttonhead screw from [McMaster-Carr](https://www.mcmaster.com/92095a184) or [Bolt Depot](https://www.boltdepot.com/Product-Details.aspx?product=7222)
    - purchase 1x D2HW-BL201H from [Digikey](https://www.digikey.com/products/en?keywords=D2HW-BL201H)
    - Optional: replace the sixteen M3, 12mm buttonhead screws for bolting in the rail with M3, 10mm screws instead
- Adjusted Parking Post for the default extruder such that the tool doesn't twist while being picked up. Updated [assembly instructions](https://github.com/machineagency/jubilee/blob/master/tools/jubilee_tools/tool_posts/configurable_tool_post/assembly_instructions/parking_post_assembly_instructions.p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)
- Adjusted the Carriage Back Plate and pulley spacers such that the nominal position of both belts is coplanar, rather than slightly off. Fixes [Issue #14](https://github.com/machineagency/jubilee/issues/14).
- swapped M3 nuts and for heat set inserts int the Carriage Back Plate to add clearance for the aluminum crossbar upgrade.
- Updated the instructions to show how to properly install the composite _Keep Nuts_ into the carbon fiber crossbar. Fixes [Issue #15](https://github.com/machineagency/jubilee/issues/15).
- Re-exported latest STL files for Extruder Tool
- Added an "Upgrades" folder for alternate frame components
- Tweaked direct drive extruder to fix compatibility issue when assembling for a V6 hotend.
- Adding Heatsinks to default extruder BOM for the stepper motors as they can get hot enough to warp the tool plates

The following parts *must* be reprinted since rel/jubilee-1.0:
- CPB-02 [Carriage Back Plate](https://github.com/machineagency/jubilee/blob/master/frame/fabrication_exports/3d_printed_parts/toolchanger/toolchange_carriage/carriage_back_plate.STL)
- [Belt Clasp](https://github.com/machineagency/jubilee/blob/master/frame/fabrication_exports/3d_printed_parts/frame/belt_clasp.STL)
- PPS-02 [Printed Pulley Spacer](https://github.com/machineagency/jubilee/blob/master/frame/fabrication_exports/3d_printed_parts/frame/printed_pulley_spacer.STL)
- PPB47-03 [Parking Post Base](https://github.com/machineagency/jubilee/blob/master/tools/jubilee_tools/tool_posts/configurable_tool_post/fabrication_exports/parking_post_base_47mm.STL)
- TH47-03 [Tool Holder](https://github.com/machineagency/jubilee/blob/master/tools/jubilee_tools/tool_posts/configurable_tool_post/fabrication_exports/tool_holder_47mm.STL)

The following parts were tweaked, but do not need to be reprinted if you have already assembled your machine.
- LMS-03 [Left Motor Plate Spacer](https://github.com/machineagency/jubilee/blob/master/frame/fabrication_exports/3d_printed_parts/frame/left_motor_corner_bracket_spacer.STL) has a bumper feature to make the y rails easier to install in a consistent spot.
- RMS-04 [Right Motor Plate Spacer](https://github.com/machineagency/jubilee/blob/master/frame/fabrication_exports/3d_printed_parts/frame/right_motor_corner_bracket_spacer.STL) has a bumper feature to make the y rails easier to install in a consistent spot.

### Minor Fixes/Tweaks
- Most printed parts now have part numbers with the revision id on them. This feature is useful for identifying what version of a part you have to decide whether you need to upgrade to a newer revision in the future
- Fixed old V1-related graphics in Remote Elastic Lock Instructions. Some photos are still out of date, but the whole is useable in its current state.
- Reorganized file structure to clearly separate tools from frame
- M3 Drop-in T nuts have been replaced with M3 Slide-in T nuts, which are cheaper and less of a hassle to install.
- Y axis limit switch was moved forward by 0.2mm to ensure that it clicks even on poorly printed parts.

## rel/jubilee-2.0 - Jan 15, 2020

### Added
- Jubilee V2, *Cubilee*
- New [Bill of Materials](https://docs.google.com/spreadsheets/d/1pRzBQxVzL9c4T9b1RrKvSjlSwJJhJ7NcbSV6iJUv0X0/edit?usp=sharing). All parts that were added, changed-in-size, or increased in value since the V1 BOM are highlighted in yellow.

### Changed
- Frame was adjusted to accommodate larger tools and a build volume of 300x300x300mm. Size update also fixes issue [#4](https://github.com/machineagency/jubilee/issues/4)
- Dowel pin spacing on the Coupling Plate was modified slightly to more easily lock E3D tool plates
- Back Panel bolt hole pattern now accommodates either a set of Duet2 + Duex5 boards or a set of Duet3 + 2 expansion boards + Raspi 
- Front opening has more clearance for bed plate removal 
- ZYLTech Leadscrews are now 375mm instead of 270mm
- Side Panel Sizes are slightly larger
- Back Panel Size is slightly larger
- Crossbar Size is slightly longer. New [DXF](https://github.com/machineagency/jubilee/blob/dev/jubilee_2.0/fabrication_exports/machined_parts/crossbar/crossbar_6mm_for_400mm_mgn12_rail.DXF)
- Belt lengths are now slightly longer
- X-axis MGN12 rail is now 400mm instead of 350mm
- Z-axis MGN12 rail is now 400mm instead of 300mm
- 3D Printed Feet are now easier to assemble and ~$30 cheaper
- Mounting plates for Z axis motors are now one piece each instead of two.
- All M2 Dowel Pins were replaced with set screws for easier assembly.
- Toolchanger Elastic Lock Actuator was redesigned for ease of assembly. Using a V1 lock will still work though
- The BOM lists the embedded magnet build plate as the default since it fixes issue [#3](https://github.com/machineagency/jubilee/issues/3)

The following parts *must* be reprinted since Release 1.0.0:
- [Front Left Bed Coupling Lift](https://github.com/machineagency/jubilee/blob/master/fabrication_exports/3d_printed_parts/frame/front_left_bed_coupling_lift.STL)
- [Front Right Bed Coupling Lift](https://github.com/machineagency/jubilee/blob/master/fabrication_exports/3d_printed_parts/frame/front_right_bed_coupling_lift.STL)
- [Front Left Z Motor Plate](https://github.com/machineagency/jubilee/blob/master/fabrication_exports/3d_printed_parts/frame/front_left_z_motor_plate.STL)
- [Front Right Z Motor Plate](https://github.com/machineagency/jubilee/blob/master/fabrication_exports/3d_printed_parts/frame/front_right_z_motor_plate.STL)
- [Back Z Motor Plate](https://github.com/machineagency/jubilee/blob/master/fabrication_exports/3d_printed_parts/frame/back_z_motor_plate.STL)
- [Carriage Coupler Plate](https://github.com/machineagency/jubilee/blob/master/fabrication_exports/3d_printed_parts/toolchanger/toolchange_carriage/carriage_coupler_plate.STL)

The following parts have minor changes, but do not need to be reprinted:
- [Left Motor Corner Bracket Spacer](https://github.com/machineagency/jubilee/blob/master/fabrication_exports/3d_printed_parts/frame/left_motor_corner_bracket_spacer.STL)
- [Right Motor Corner Bracket Spacer](https://github.com/machineagency/jubilee/blob/master/fabrication_exports/3d_printed_parts/frame/right_motor_corner_bracket_spacer.STL)
- [Left Double Pulley Corner Bracket](https://github.com/machineagency/jubilee/blob/master/fabrication_exports/3d_printed_parts/frame/left_double_pulley_corner_bracket.STL)
- [Right Double Pulley Corner Bracket](https://github.com/machineagency/jubilee/blob/master/fabrication_exports/3d_printed_parts/frame/right_double_pulley_corner_bracket.STL)
- [Front Left Leadscrew Retainer](https://github.com/machineagency/jubilee/blob/master/fabrication_exports/3d_printed_parts/frame/front_left_leadscrew_retainer.STL)
- [Front Right Leadscrew Retainer](https://github.com/machineagency/jubilee/blob/master/fabrication_exports/3d_printed_parts/frame/front_right_leadscrew_retainer.STL)
- [Back Leadscrew Retainer](https://github.com/machineagency/jubilee/blob/master/fabrication_exports/3d_printed_parts/frame/back_leadscrew_retainer.STL)
- [Back Bed Coupling Lift](https://github.com/machineagency/jubilee/blob/master/fabrication_exports/3d_printed_parts/frame/back_bed_coupling_lift.STL)
- [Front Left Foot](https://github.com/machineagency/jubilee/blob/master/fabrication_exports/3d_printed_parts/frame/front_left_foot.STL)
- [Front Right Foot](https://github.com/machineagency/jubilee/blob/master/fabrication_exports/3d_printed_parts/frame/front_right_foot.STL)
- [Back Left Foot](https://github.com/machineagency/jubilee/blob/master/fabrication_exports/3d_printed_parts/frame/back_left_foot.STL)
- [Back Right Foot](https://github.com/machineagency/jubilee/blob/master/fabrication_exports/3d_printed_parts/frame/back_right_foot.STL)

### Removed
- Delrin Slip Face on toolchanger elastic lock

## [1.0.0] - 2019-09-09

### Added
- Jubilee V1, *the original Jubilee*
- Original [Bill of Materials](https://docs.google.com/spreadsheets/d/1gq5yLxlfPtb3yrGsuXR_ZLhAFGB77CzGvfcWYyYIvT4/edit#gid=0)

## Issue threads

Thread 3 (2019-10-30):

Jubilee's Bed plate (with BuildTak) takes ~5-to-8 minutes to finish thermally expanding

Poofjunior, 2019-10-30:
Although the silicone heater can reach 60C from ambient in about 1 minute, the combined thermal mass of the aluminum bed and the Buildtak magnetic plate take about 5 minutes to finish thermally expanding. During this time, the printer will expand vertically about 0.1mm--enough to make-or-break a first layer.

If the machine is zeroed while the bed is cool and the print is started before the machine has finished thermally expanding, the first layer risks ripping as the bed-to-nozzle distance will eventually become too close to the bed.

A first pass at fixing this issue would be to zero the Z height at the start of the print after bed has reached temperature. However, since the sensor is on the _underside_ of the machine, this does not provide an accurate estimate of the temperature of the entire plate at steady state.

A slightly-better fix would be to decrease the thermal mass of the aluminum bed plate. This fix is being tested now as a future revision of the Jubilee bed plate will feature magnets embedded in the build plate. This updated plate will remove the added thermal mass of the Buildtak magnetic surface.

Another slightly-better solution would be to measure the temperature closer to the print surface. The Railcore bed plate puts the bed sensor in a pocket on the top of the build plate, not the bottom. Jubilee could adopt this solution.

For now, the surefire way to work with this issue is to (1) heat the bed, (2) wait 5 minutes, (3) zero the z and begin printing.

This issue will get an update as soon as the new beds with smaller thermal mass are tested.

KodinLanewave, 2020-01-20:
Why not modify the design by drilling a hole in the center of the bed plate, (prior to putting any surfaces on it, and maybe countersink both sides of the hole to eliminate burrs, etc...) then submerge the thermistor in thermally conductive epoxy?  Might give you a better indication of the plate temperature rather than just the silicone heater temperature.

Poofjunior, 2020-01-20:
Aye; this is similar to the last suggestion. It's a bit of extra work that I'd love to avoid burdening the user with if possible. I'll have some more updates on this issue this week, but it also seems like the embedded magnet plate heats up wayy faster (less than 4 minutes).

KodinLanewave, 2020-01-20:
No one has done a spring steel (coated or otherwise) build surface with integrated thermal sensor(s) yet, right?

Poofjunior, 2020-01-20:
Hmm, Not that I know of. Are you envisioning a particular sensor in mind?

KodinLanewave, 2020-01-20:
No, just spitballing ideas; For safety you'd want to still monitor the sensor in the silicone heater, (especially if you're using one of the higher wattage A/C heating pads due to the fire danger) but the critical temperature measurement for printing is as close to the print surface as possible; why not have one directly integrated into the print surface if you're going so far as to design an entire machine?  Just a thought, no idea how practical it'd be to implement.  Still think the 1/4" hole in the middle of the thicker build plates make more sense both from a implementation standpoint and a design standpoint.  CAD files can be updated for those that are making bed plates, anyone who already has one probably either owns or can gain access to a drill and drill bit and some JB-Weld epoxy.

Poofjunior, 2020-01-20:
Gotcha. Yeah; before I go the "invasive" route, I'm going to start with a bolt-on terminal lug thermistor.
https://www.digikey.com/product-detail/en/vishay-bc-components/NTCALUG01A103F/BC2891-ND/4896928
This seems to be an industrial standard for measuring plate temps that I haven't seen (yet) on printers. Best of all, it can be screwed into an existing threaded hole.

I plan on checking how well both thermistors track against some "ground truth" measurements from the top.

KodinLanewave, 2020-01-20:
Oh interesting. Might want to add some silver thermal paste, (or equivalent,) between the mating parts to minimize conduction losses.

Poofjunior, 2020-01-20:
Stay tuned, and I'll keep everyone posted on how it goes!

Poofjunior, 2020-01-23:
Ok I'm calling this a mystery solved.

Using an IR gun to monitor the top plate temperature, I ran two setups. Both had
* magnetic plate
* keenovo heated pad
* calibrated with the thermistor they were using

one had the *built-in* thermocouple and one had the *bolt-on* thermocouple.

## Built-In Case
The built-in thermocouple measures 21C to 60C in 1:15, but at the 1:15 mark, the IR gun measures the top surface to still only be 45-47C. After 5 minutes, the built-in thermocouple and IR gun agree at about 60-61C

## Bolt-On Case
The bolt-on thermocouple measures 21C to 60C in about 2:15. The plate temp overshoots by about 3-5C at this time but cools to 60-61C in about 5 minutes.

## The Verdict:
Use the bolt-on thermocouple. Even though it lags behind the true plate temperature, it guarantees that the plate wont keep expanding when a print has started. Waiting 120 to 180 seconds is also super quick by comparison with most printers.

Bonus: it's like $2-3 and detachable, so it's easy to replace.

The BOM and instructions already point to using the embedded mag plate and the bolt on thermocouple, so I'm marking this issue resolved.

Closed 2020-01-23.

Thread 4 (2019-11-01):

Default tool size limits maximum bed size to 290 in Y

Poofjunior, 2019-11-01:
This picture says it all.

https://media.discordapp.net/attachments/627988602269335568/639674827103273000/IMG_0850.jpeg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

Essentially, the default tool's thickness limits the print area in the y direction to about 290mm in a multitool printing setup.

DanalEstes, 2019-11-01:
I believe this can be resolved by making the right and left rail of the upper frame longer, thus moving out the "upper front" rail that carries the tools, moving it in the Y direction.  It looks like we need about 15 to 20 more mm. Relocate the front R/L pulley assemblies by the same amount. That implies longer belts. I don't believe any other part of the printer would have to change, in a "retrofit" situation. Not even the linear slides.

solhuebner, 2020-02-09:
@DanalEstes As this was implemented in 2.0, can this issue be closed?

Poofjunior, 2020-02-09:
@solhuebner aye!
This is fixed as of rel/2.0
https://github.com/machineagency/jubilee/blob/master/CHANGELOG.md#reljubilee-20---jan-15-2020

Closed 2020-02-09.

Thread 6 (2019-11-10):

Suggestion for auto tool offset and autotraming.

TypQxQ, 2019-11-10:
I went trough the design and I have a suggestion for an autolevel that would detect the offset of any tool and tram the buildplate.

Using a dummy tool with only a PrecisionPiezo and a known length from the anchoring point of the toolchanger to the dummy "nozzle" one can tram the bed and set Z to 0.

Using a microswitch sensor on a platform controlled by a stepper and a lead screw, one can set the height difference between the known dummy tool and any other tool.
The toolchanger in the startup routine can change Z to the small leveling platform, Home Z with the dummy by raising the platform until it hits the microswitch. Next, changing the tools, it can set the offset for each and every tool with M585.

It can then lastly home and tram the real bed with individual lead screws.

Perfect for changing nozzles. Only the X/Y offset has to be known.

I considered another Piezo for the platform but they are too sensitive to Z movement.

KodinLanewave, 2020-01-20:
Another option is design a "zero-set" tool offset ...setter.  Basically just a simple tool head carrier with a z-screw and a piezo sensor.  When you build or modify an existing tool, set it on the device, activate it, and it lowers the head down to the piezo sensor, then records the offset into whatever tool table entry you designate.  Think of it like a tool probe offset fixture on a CNC mill, just not bolted to the machine.  Probably complete overkill, but it'd be both fast and easy to build or modify tools without spending an hour getting the offsets perfect.  I'm not even sure you'd need the stability of a full linear rail since you're just measuring Z offset length. Just a length of aluminum extrusion, a really short leadscrew, a stepper, some wheels designed to run along aforementioned extrusion, and the piezo sensor, along with whatever rendition of the tool changer lock mechanism (can be hand-actuated to keep cost down) makes sense.

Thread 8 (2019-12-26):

Where is the Top Lock Actuator Plate?

vcapra1, 2019-12-26:
In the assembly instructions (page 2 of [toolchanger_lock_assembly_instructions.pdf](https://github.com/machineagency/jubilee/blob/master/assembly_instructions/toolchanger_mechanism/toolchanger_lock_assembly_instructions.pdf)), it says a "Top Lock Actuator Plate" is needed.  There is no such part in the list of 3d printed parts.  The closest thing I can find is the "Lock Actuator Base Plate", which is referenced on the following page and does in fact exist in the list of 3d printed parts.

The image of the Top Lock Actuator Plate does not match the 3d model, but the model does match the Lock Actuator Base Plate on the following page.  In the first case, there are 2 more holes and 2 slots in the side of the part, which don't exist on the next page, or the 3d model.  Am I to assume these are in fact the same part, and those holes/slots are not necessary?

timcurtis67, 2019-12-27:
I believe the part you are looking for is really called "top_lock_actuator_plate_Spring Guide Anchor Block.stl" or .sldprt. Here is a copy of that file.

All of the holes are used, the extra holes you see are to bolt this part to the base plate.
[top_lock_actuator_plate_Spring Guide Anchor Block.zip](https://github.com/machineagency/jubilee/files/4005157/top_lock_actuator_plate_Spring.Guide.Anchor.Block.zip)

vcapra1, 2019-12-28:
That is not what I meant.  The assembly instructions show the following part:
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
But this is the actual 3d model of that part:
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
As you can see, there are two holes missing from the 3d model, as well as the ziptie slots. on the side.  These holes are where the spring guide anchor block is mounted, so now I can't attach that piece because the holes are missing.

vcapra1, 2019-12-29:
I'm closing this issue as it appears the guide block isn't necessary, so the missing holes are not a problem.

Closed 2019-12-29.

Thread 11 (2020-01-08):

BOM - Part numbers w/ ver. Embed part number in printed parts

BryanHaven, 2020-01-08:
Include a field in the BOM for part numbers
Part identifier should reference the assembly the part is used in
Part numbers should have version reference
Engrave/emboss part number in printed parts so when printed part number is visible
Add part numbers to machined parts - fabricator may determine best method for marking of part (laser etch, stamped, machined, etc.)

Poofjunior, 2020-01-23:
Ok, we currently have a Shopping list, not a proper BOM, but I can export one pretty easily, that we can group into subassemblies.

Itemizing from above, it looks like part numbers should have:
* some cross-reference to the sub-assembly that it belongs to.
* unique numerical identifier
* part revision
* part process (*P*rinted, *L*aser cut, *M*achined, *V*itamin etc.)

Here are some special cases to consider:
* interchangeable parts. Is there a way we can quickly identify by part number whether or not something is a replacement for something else? Example: a metal crossbar and an aluminum crossbar are functionally the same thing.
* Parts that are configurable. Example: on the parking posts, the width of the unit is parametric, enabling us to generate a range of sizes depending on the tool. We might be able to tack on the parameter value at the end of the part number.

BryanHaven, 2020-01-23:
https://grabcad.com/tutorials/3d-printing-design-guidelines
Posting reference for lettering best practices - mostly so I don’t forget.

laudiblellc, 2020-01-23:
I would recommend including the part dimensions' dependence on printer
size, or at least print volume size. The hypercube Evo bom does this and
makes customizing your printer very easy.
Saul

On Thu, Jan 23, 2020 at 12:08 AM BryanHaven <notifications@github.com>
wrote:

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
--
Thanks,
Saul
Laudible LLC

Poofjunior, 2020-01-23:
@BryanHaven and @laudiblellc I think you're both getting at "part  printability" with your later discussion points. Some of these are actually already called out in the [Design Objectives](https://github.com/machineagency/jubilee/wiki/Project-Goals#design-objectives) doc, but I could flesh out some details such that others can contribute back parts that are modeled in the same spirit.

BryanHaven, 2020-01-23:
@Poofjunior True, primarily I woke up vaguely remembering something I’d read and wanted to get it down somewhere useful. In this case specifically related to etching or embossing text into a printed part. It’s easy to make the part numbers legible on screen but harder when you print them.

Poofjunior, 2020-01-29:
Ok, here's a pass at a part numbering scheme for all non-stock parts.

**[who designed it] - [fab process + material] - [uniqueid] - [revision] - [who fabricated it]**
* **[who designed it]** 3 characters. I'll claim **PJR**, short for poofjunior. This is a nice way to credit folks. If we add stuff to the repo, they get a part number that references them. It also helps us trace design-related bugs and points us to who we can ask for help debugging. If mulitple people design it, we can use **MIX**
* **[fab process + material]** 3 characters
    * **M**achined
        * **M6** MIC6 aluminum
        * **61** 6061 aluminum
        * **K1** K100S aluminum
        * **A5** ATP5 aluminum
        * **C**arbon **F**iber
    * 3D**P**rinted
        * **PL** PLA
        * **PE** PETG
        * **CP** **C**arbon filled **P**LA
        * **CE** **C**arbon filled P**E**TG
    * **L**aser cut
        * **DE**lrin
        * **AC**rylic
        * **PL**ywood
* **[unique id]** 3-9 characters. 3 preferrable. Up to 9 to denote special configurations/mirrors
* **[revision]** 2 characters revision number
* **[who fabricated it]**
    * **713**Maker
   * **C**NC **M**a**D**ness
    * **S**ee**M**e**C**NC
    * **M**andala **R**ose **W**orks
    * **MIS**umi
    * **YOU** make it yourself by default. (3d printed parts)

Here are some examples:
* PJR-MCF-CRO-01-CMD
    * [poofjunior] designed a [Machined] [Carbon Fiber] [Crossbar] [revision 1] manufactured by [Mandala Rose Works]
* PJR-MK1-CRO-01-MRW
    * [Poofjunior] designed a [Machined] [K100S] [Crossbar] [Revision 1] manufactured by [Mandala Rose Works].
* MIX-MM6-BED-01-713
    * [Poofjunior and 713Maker] designed a [Machined] [MIC6 aluminum] [bed] [revision 1] manufactured by [713Maker]

This numbering scheme has some tradeoffs. The main one is that it doesn't have a reference to the subassembly. I don't think we *really* need it since we have less than 10 top-level subassemblies and we can almost-certainly deduce what fabricated part was made based on the unique id.

But it also has some major benefits, I imagine that folks will build a Jubilee with parts sourced from various places. Knowing how someone configured their particular Jubilee is extremely useful for helping us figure out how to help them debug an issue. For example: I imagine that the aluminum crossbar will have a different top speed than the carbon crossbar. I also imagine that a carriage made from PLA will have different maximum temperature rating compared to PETG. What's more, we can also invert the supply chain and ask them to stock specific part numbers. (Example: we could ask CNC Madness to stock PJR-MCF-CRO-01-CMD. That way people who want a carbon crossbar can just ask for PJR-MCF-CRO-01-CMD instead of emailing him a DXF file with material specs.)

Ok, what do people think?

Enza3d, 2020-01-29:
I like the content of the above part #'s
I would argue the Creator of the part should go on the end of the part number to aid in listing items alphabetically in a coherent fashion.  Ideally the most relevant piece of information is listed as the first thing in the string so it can be sorted by that parameter.

At work we start our Main assemblies with 00 so it always appears as the first item in a list. The sub assemblies are followed by 01,02,03 etc...
Then the parts are 101,102,103... for the parts in the 01 sub assembly.  201,202,203 for parts in the 02 assembly.

Since we do consulting work every project has an Identifier code which syncs our sales team with the engineering team.  This 4 Digit number is at the front of every single project file we create.   So a full main assembly would look like 4010-00.SLDASM, a part would look like 4010-105.SLDPRT

We actively chose not to capture any other information in the part number to keep it light weight and easy to understand.  We dont do any real fabrication or sourcing though so we dont need to bake as much info into our Part #'s.

tsunaminaut, 2020-01-29:
Agreed about using main assemble numbers first then part of assembly second, I use a similar scheme when saving media i label them as last 2 digits of year, followed by month and then date so when viewed in a file they will organize by year then month then date and be in a logical order and easy to find.

Enza3d, 2020-01-29:
I will add, the simplicity of a part numbering scheme is often directly corelated to the compliance, if its too complicated (need a decoder ring to unscramble) people will tend to "forget" to use it, where if its just the bare minimum people will follow it.  The whole thing should be easy to memorize and simple to figure out without a Key

BryanHaven, 2020-01-29:
I’d also add that if we’re looking at etching / embossing the part number into the printed and machined parts they shouldn’t be but so long. A vendor cross-reference chart may be a solution to the simple part number for the project and vendor specific SKUs.

Sent from my iPhone

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

Poofjunior, 2020-01-29:
Thanks for the feedback!

To trim length, I can probably drop the "who-designed-it" field and re-order the fields so that the initial bit is more relevant so it looks like:

**[uniqueid] - [revision] - [fab process + material] - [who fabricated it]**

In cases where machinists add their own insignia, we can drop the last bit so it looks like:

**[uniqueid] - [revision] - [fab process + material]**

Finally for printed parts, we could display just embed the first two bits:

**[uniqueid] - [revision]**

As far as unique id goes, **[subassembly] - [number]** is one option. Some parts have configurations, though, and it would be nice to capture some of the configuration parameters in this section. Here's an example.

The tool holder is parametric, where the spacing is configurable to handle wider or skinnier tools. The default has 55mm center-to-center hole spacing.
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

But we could easily change that to be 65mm:
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

Anyone have any thoughts on configurable parts?
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
Enza3d, 2020-01-29:
We add a two digit code at the end of our part numbers which denotes the configuration, so 3333-101-00 denotes the default config, 3333-101-01 denotes the first configuration of part 101.

 I dont particularly care for this approach but we haven't been able to come up with something better.

Poofjunior, 2020-01-30:
Ok, I have an updated draft that incorporates sub-assembly numbers. How does this look?

## Part Numbering Scheme
The part numbering scheme is as follows:

**[subassembly] - [part id + params] - [revision] - [fab process + material] - [who fabricated it]**

For 3D printed parts, only the short numbering scheme will be used.

**[subassembly] - [part id + params] - [revision]**

Here's the breakdown of what these mean.

* **[subassembly]** what lowest-level subassembly does this belong to?
    * 00 top level assembly
    * 02 motor corner plates
    * 03 double pulley corner plates
    * 04 toolchanger elastic lock assembly
    * 05 electronics back panel
    * 06 side panels
    * 07 toolchanger carriage component assembly
    * 09 Build Plate Assembly
    * ?? Lower Frame Assembly
    * 01 corexy frame assembly
    * 08 Z axis assembly
* **[part id + params]** 3-9 characters. (Uppercase) letters and numbers only. Try to keep these around 3 characters while the rest are reserved for parameters. Here are some common ones.
    * **EXT409** -- extrusion of length 409mm
    * **CRS** -- crossbar
    * **BED** -- bed plate
* **[revision]** two digits increasing from 0
* **[fab process + material]**
    * **M**achined
        * 60**61** aluminum
        * **K**100**S** aluminum cast tool plate
        * **M**IC**6** aluminum cast tool plate
        * **A**TP**5** aluminum cast tool plate
    * 3D**P**rinted
        * **PL**A
        * **PE**TG
        * **C**arbon Fiber impregnated P**L**A
        * **C**arbon Fiber impregnated P**E**TG
    * **L**aser cut
* **[who fabricated it]** This can be an open field in the scheme that can be used by the machinist. Otherwise, here are some defaults.
    * **M**i**SU**mi
    * **713**Maker
    * **S**ee**M**e**C**NC
    * **M**andala **R**ose **W**orks

### Blacklisted Letters
Let's not use these letters: i, o

This is also in a draft here:
https://github.com/machineagency/jubilee/wiki/Part-Numbers

Kirinkunhime, 2020-02-01:
I want to suggest a minor addition to this: And that is that all part-numbers should be written with capitalletters only. (As is already implied)

This should help improve readability, and also the letter l might be too similar to a 1 otherwise.

Poofjunior, 2020-02-02:
Thanks @Kirinkunhime! Adding this to a note on the bottom of the current doc.

Poofjunior, 2020-02-10:
Ok, I think I managed to go through and capture most suggestions here. Short part numbers (with revision IDs) are now embedded in their respective parts for printed parts. Full part numbers are specified in the wiki doc linked above.

These are driven from metadata attached to each part, so exporting these to a spreadsheet in the future should be pretty straightforward.

Poofjunior, 2020-02-10:
Oh, here are some examples:
[front_left_foot](https://github.com/machineagency/jubilee/blob/master/frame/fabrication_exports/3d_printed_parts/frame/front_left_foot.STL)
[right motor plate](https://github.com/machineagency/jubilee/blob/master/frame/fabrication_exports/3d_printed_parts/frame/right_motor_plate.STL) (see underside)

Closed 2020-02-10.

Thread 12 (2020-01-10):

Possibility to add a universal disconnect system to make tools quick swappable

Chase4306, 2020-01-10:
How hard would it be to add a disconnect to allow a tool to be unplugged, and then another to be plugged in its place? into the same port even. maybe using a plug like this to allow some high current pins (heaters, laser cutter) and plenty of low current pins for thermistors and sensors https://www.molex.com/molex/family/ten60_form.jsp

LittleHobbyShop, 2020-01-12:
There are a few projects like this in existence already. This is one that I will be using, I've already had the boards made and have populated but haven't put into use yet. D-SUB Connector and hole pattern to match a NEMA17.
https://www.hackster.io/viktorsilivanov/quick-swap-board-for-3d-printer-hotend-fb26e4
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
I'm not confident of the reliability of push/quick release/magnetic contacts for this kind of application. I'd rather have something more secure like the D-SUB used above.

DUET are also releasing tool boards soon (within a few weeks according to forum) for use with the DUET 3 mainboard. If you have a DUET 3 this is the way to go. Only 2 connectors to replace a tool.
https://duet3d.dozuki.com/Wiki/Duet_3_Tool_Board

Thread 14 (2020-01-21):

Belts are Slightly Non-Coplanar

Poofjunior, 2020-01-21:
Both the printed pulley spacers and the carriage back plate raise the belt out-of-plane, putting both of them at a slight angle. During the assembly, this issue can be corrected by eyeballing the parts into the right spot, but it would help if the nominal location were correct....

Poofjunior, 2020-01-21:
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

Ok, spacing is now fixed. Nuts have also been removed and replaced with heat-set inserts. Given that most folks are still buying these in 100 packs, this bom tweak shouldn't hurt anyone. (Swapping nuts for inserts also makes more space for the aluminum crossbar upgrade.)

Poofjunior, 2020-01-21:
This is now up-to-date in master.

Closed 2020-01-21.

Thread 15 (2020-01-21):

Crossbar Keep Nuts Wiggle when installed improperly

Poofjunior, 2020-01-21:
The crossbar's [Keep Nuts](http://www.npfasteners.com/composites/keep-nut-kn.htm) require an axial pull-out force to get their teeth to properly engage. Otherwise, shoulder screws attached to them will wiggle.

The easiest fix for this is to simply screw in an M4 screw with a stack of washers into the Keep Nut with a sufficient amount of torque such that the teeth engage; then, remove the M4 screw and washer stack and resume normal assembly. This needs to be added to the instructions.

Poofjunior, 2020-01-23:
Ok, there are now instructions telling folks to temporarily tighten an M4 screw and spacer into the assembly in order to get the teeth to fully engage.
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

Closed 2020-01-23.

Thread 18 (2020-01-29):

Carriage Pulley missing in the insert instructions

Poofjunior, 2020-01-29:
In the new heat-set insert instructions, the carriage pulley is missing.

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

Poofjunior, 2020-01-29:
issue already exists here:
https://github.com/machineagency/jubilee/issues/17

Closed 2020-01-29.

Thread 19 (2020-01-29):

Outer Frame Assembly and Alignment Instructions

cindygfeng, 2020-01-29:
Sheet 2: We had some confusion on which way the brackets go in.  Include a statement that says that the interior inside corner brackets are directional, and they go on the 604 mm TSlot Extrusion first

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

Poofjunior, 2020-01-29:
Sure; I can change the first word chunk to say:

_First slide the brackets into the long extrusions. Then fit the remaining parts together as shown above without tightening down any screws. Lay the loose assembly on a flat surface._

_Note that only one side of the bracket is meant to completely slide into the extrusion._

Poofjunior, 2020-01-30:
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

How about this?

Poofjunior, 2020-02-20:
Closing; I think this should be sufficient.

Closed 2020-02-20.

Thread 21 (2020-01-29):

Outer Frame Assembly and Instructions

cindygfeng, 2020-01-29:
Sheet 6 of 11: We found it easier to slide the L brackets onto the shorter 409 mm TSlot Extrusions first, keeping in mind the direction of the L brackets.  Then slide all 4 onto the 604mm long extrusions.

Also circled the two middle L brackets that we forgot again.

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

Poofjunior, 2020-01-29:
I will definitely make a note of this. Thanks for the heads up.

Closed 2020-12-03.

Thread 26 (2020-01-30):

Warping Extruder Tool Plates

Poofjunior, 2020-01-30:
It's unclear whether this is coming from the hotend or the bed, but the excess radiated heat is causing these to warp over time.

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

They seem to settle after a bit which is why I never noticed this and probably just recalibrated the heads months ago.

These are made from PLA by default. I will start by giving these a go in PETG.

Poofjunior, 2020-02-10:
Reprinted from PETG.

It turns out that the source of error appears to be a rather hot extruder stepper motor, which will affect even the PETG plates. However, adding a [heatsink](https://www.amazon.com/gp/product/B07FNK2866/ref=ppx_yo_dt_b_search_asin_title?ie=UTF8&psc=1) to the back appears to drop the temperature down to about 48C and prevent further warping.

I will continue to run the machine in this state for a bit longer before calling it a problem-solved.

Poofjunior, 2020-02-20:
This is definitely due to a hot extruder motor. Printing material doesn't really matter as long as the heatsink is applied. The heatsink is now in the extruder BOM.

Poofjunior, 2020-09-09:
It looks like ambient radiation is still having an effect on tool plates. Here's a PLA plate built to the current spec by @guildner

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

matthewSorensen, 2020-09-09:
Definitely still an issue, and seemingly independent of the heater block orientation. Since it's not a universal complaint, I wonder how much it depends on the specific filament the plate was printed in, and the workload of the tool?

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

guildner, 2020-09-09:
Additional information: my bed temperature was at 80C, and the extruder was at 235C. The print job was long, like 13 hours, and flat and close to the bed surface for a large portion of the print time. (large flat objects that took up most of the build plate.)

Poofjunior, 2020-09-09:
I think the remaining causes on this issue could be:

- ambient radiation from the hotend or bed
- creep from the axial force applied by the twist lock
- the combination of both

A metal plate will fix all of these issues. That said, it it's just ambient radiation, it would be nice to have some sort of heat shield (tape) solution that wouldn't necessitate metal parts in the minimum viable design. That said, maybe I'm asking too much since we're dealing with a system that's producing heat to melt plastic precisely in the first place ;)

guildner, 2020-09-09:
@matthewSorensen what materials (bed temp) do you usually use? Did yours warp after a particularly long or hot print? Or is that something that progressed over time?

This may not be as much of a problem for lower bed temperatures, or prints that are only close to the bed for a shorter amount of time... just thoughts.

Blade765, 2020-09-10:
What about just using a material rather than PLA? Maybe even heat treated HTPLA? I think the deflection temp after heat treating is 150ish? Granted, requiring a special material for the plates is an added expense, but it would still be significantly cheaper than metal.

Blade765, 2020-09-11:
I was referring to Proto-Pasta's Carbon Fiber HTPLA. Once heat treated, its good for up to ~160*C.

Poofjunior, 2020-12-03:
Ok; the current default points to getting a [metal version of this plate](https://shop.guildtek.com/index.php?main_page=product_info&cPath=1&products_id=4).

I think it's time to close this issue and reopen another one asking for a simpler fix that doesn't necessitate such a complicated metal part. I don't want to jump to far and mandate metal plates for tools, but this design should hold us over at least until we come up with something better to replace it.

Closed 2020-12-03.

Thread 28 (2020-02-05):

Lower Frame Assembly instructions - Back Z Motor Plate Assembly 2

kelliead, 2020-02-05:
Lower Frame Assembly instructions, sheet 6 of 14, Back Z Motor Plate Assembly 2

Add note that says which direction the wires on the motor go (if it matters).
Specify to put the dab of threadlock on the tip threads of the screws.

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

Poofjunior, 2020-02-06:
Wire notes and threadlock note added!

Closed 2020-02-06.

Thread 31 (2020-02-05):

Lower Frame Assembly instructions - Z Plate Tightening

kelliead, 2020-02-05:
Lower Frame Assembly instructions, sheet 13 of 14, Z Plate Tightening

Add dimensions for correct placement of back Z plate using a ruler. 15.5cm from edge of plate to inside edge of side extrusion.

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

Poofjunior, 2020-02-06:
Ok, so it turns out that I did add this info--I just never exported it--doh!

Poofjunior, 2020-02-06:
@kelliead @awaer @cindygfeng actually this is already fixed and pushed online. make sure you're working off the latest instructions on the web, not a local copy that you downloaded.

cindygfeng, 2020-02-08:
@Poofjunior We were working off of instructions that we printed that day from the Assembly Instructions wiki page.  Perhaps the link hadn't been updated, and that's why we had old instructions? @kelliead

Closed 2020-02-06.

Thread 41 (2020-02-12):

Build plate assembly instructions: bed orientation is missing

awaer, 2020-02-12:
Sheet 4 of 13 is missing an annotation to indicate bed orientation (see example), which could prevent some users from erroneously installing the M3 screws on the wrong side.

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

Poofjunior, 2020-02-20:
this is now up to date!

Closed 2020-02-20.

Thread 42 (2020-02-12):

CoreXY Frame Assembly Instructions: Toolchanger Locking Mechanism Items

BryanHaven, 2020-02-12:
Assembling the spring guides and sheath before running wire rope through the spring guides.
Run two 600mm spring guides through nylon sheath (1/8" was used and worked).
Leave 25 mm of spring guide exposed on the carriage end and 55 mm of spring guide exposed on lock actuator end.
Ensure spring guides are even on each end.
Use adhesive lined shrink tubing is used to affix sheath to spring guide.

Spring guide anchor block not listed - very useful for managing spring guides without a third hand.

See Jubilee Day 21 Livestream @ 1:40

Poofjunior, 2021-03-16:
I think this new assembly procedure is now pretty well captured in the new instructions. Anchor Block is also restored.

Closed 2021-03-16.

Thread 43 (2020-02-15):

Inconsistent Tool Pickup

Poofjunior, 2020-02-15:
It's possible (and actually quite likely with all revisions of Jubilee so far) that the tool can be picked off the parking post in such a way that doesn't properly lock the tool into the carriage. This is because the twist lock can cause the entire to tool to twist if it snags in the wedge before pulling it into the coupling. The result is that the tool balls don't seat against the pins and are instead constrained by the wedge.

### Diagnosis:
This issue is nefarious as it can be hard to track down without an upward-pointing webcam
* Monochrome prints look perfect, but multicolor prints look like they have inconsistent extrusion issues.
* The tool may physically "jiggle" in the carriage if you try to wiggle it with your hands. However, subsequent pickups may or may not jiggle.

### Possible Fixes
There are a number of ways to fix this problem:
* stiffer spring (+ possibly a stronger motor)
    * this would overpower the twist applied to the tool and eventually get it to seat properly into the coupling.
    * this fix can be tried by shortening the current length of the spring a few mm. 103.5-to-104mm instead of 106.5mm
* better parking post
    * this would prevent the current tool from twisting as it is being picked up.
* better tool constraint upon tool pickup
    * when the tool is picked up, something could physically prevent the tool from twisting upon pickup.
        * This could simply be a parking post that prevents twist.
        * This could also be some external nesting force (spring, opposing magnets) that pushes on the tool as it is being picked up.
* smoother Wedge Plates
    * this would prevent the tool from snagging on the wedge plate and twisting as it is being picked up.
* (Other suggestions welcome!)

I'm opting to start with the second option. The current parking post is admittedly pretty crappy in that it's basically a giant pivot point

BryanHaven, 2020-02-15:
Have you updated the printing instructions for the lock plate insert to print at the lower layer height?

Poofjunior, 2020-02-15:
Oof, good point. I completely dropped the ball on extruder instructions. I just started a page (draft!) for them.

https://github.com/machineagency/jubilee/wiki/Bondtech-Direct-Drive-Extruder

DanalEstes, 2020-02-15:
I did notice the finer layers on V1 instructions and did print the plates that way.  I've noticed this same thing, and with regard to the 'wiggle', sometimes when you first touch the mounted tool it will 'pop' into place and won't wiggle after that.

At this moment, I've switched back to stainless pins, and silver balls (i.e. original spec).  I am also going to shorten my spring a bit for more torque (mine may be the slightest bit long to begin with).

I will report back when there are a few hundred or thousand tool exchanges with these updates.

Poofjunior, 2020-02-16:
@DanalEstes have a go at the [new parking post design](https://github.com/machineagency/jubilee/tree/master/tools/jubilee_tools/tool_posts/configurable_tool_post). Still need to run more than just one test, but the results look very promising. (Results at the tail end of this related issue: https://github.com/machineagency/jubilee/issues/43 )

Poofjunior, 2020-02-20:
Switching to the new parking post seems to have fixed this issue since tools can no longer easily twist while being picked up.

vcapra1, 2020-04-04:
I was having the same issue, and I'm actually using aluminum parking post blocks so there's zero room for flex there.

I tried shortening the actuator spring incrementally, but I had to take off around 6mm (total length around 100mm) before seeing any improvement.  At that point, it was extremely difficult to assemble the actuator pulleys so I didn't want to go any further with that, and the problem hadn't fully gone away.

I then tried slowing the motor down to about 50% of it's normal speed for locking (as I now see you've already updated the macro file with).  I also sanded the ramp on the wedge plates to make them smoother, but printing at a smaller layer height would also work for that.

Just figured I'd share what helped solve the issue for me in case anyone else is still experiencing this problem.

Poofjunior, 2020-04-05:
@vcapra1 Thanks for the heads-up. Would you be willing to show pics of your aluminum parking post setup? Also, do you remember if you printed the wedge plate with 0.1mm layer height?

On my end, slowing down the locking procedure, pushing into the coupling before engaging it (that's a feature that's now present in the current toolchange macros), and updating the parking post design has basically eliminated this issue on my machine, but that's not to say that there could be something design-related that is making this issue crop up. Any more info on your setup would greatly help, and thanks for chiming in!

vcapra1, 2020-04-05:
I printed the wedge plates with 0.2mm height, so using 0.1mm height might help too.  In my experience, 0.2mm layers are stronger than 0.1mm layers (not sure if that also applies for this piece though, and that could be just a configuration issue that I haven't figured out yet too).

Here are photos of my parking post setup:

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

I have thin blue shims under the blocks to adjust the height, which is a disadvantage of making this out of a single block of aluminum, but I've found the sturdiness has helped a lot.  I haven't tried the new printed parking post design, so that may also work just as well.

HaythamB, 2020-04-05:
@vcapra1 you just gave me an idea. Another approach would be some cast corners and a threaded dowel rod. Found them cheap in 6x60 here:
https://www.boneham.co.uk/Products/dowel-pins/tapped-metric-dowel-pins

The dowel would fasten to a screw through the cast bracket, and the bottom of the bracket goes into a spacer block for correct height. What do you guys think?

Poofjunior, 2020-06-29:
Update on this issue:

I have had a sample run of Delrin Wedge Plates injection molded by some manufacturers in China.
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

Prelimininary Repeatability tests look... really good.
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

I'll have a bigger batch made and get these in the hands of Jubilee component vendors. They should less than $5 US apiece.

Poofjunior, 2020-07-28:
Ok, here's another image from @erikmcclain 's printer.

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

I think it's safe to close this issue at this point. Huge win for everyone!

Closed 2020-07-28.

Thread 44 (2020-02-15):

current Parking Post design does not constrain twist

Poofjunior, 2020-02-15:
The current parking post design doesn't constrain the twist direction.

See [video](https://youtu.be/LZBDh2mFa4g).

This is an issue because the carriage twist lock will attempt to twist the extruder while pulling it in. If the tool does happen to also twist with the twist lock, it will lock incorrectly.

This issue is also connected to the reciprocal parking features on the tool geometry as well. The two grooves on the tool itself (used for the parking pins) do not constrain twist for small angles. This is because the Delrin Compression Flexure is flexible and allows for some vertical play, which is used as a leaf spring to compress the tool. Even with a perfectly rigid tool post, the problem remains that this geometry allows for some slight twist wiggle. To fix this problem for good, these squishy parts need to go.

I'll get to work drafting some new left and right parking wing designs for the extruders that use [O-rings](https://www.amazon.com/gp/product/B07GJMB5ML/ref=ppx_yo_dt_b_asin_title_o00_s00?ie=UTF8&psc=1) instead of the Delrin bits to hold the tool in place and prevent it from sliding out when the carriage retracts.

This issue is related to https://github.com/machineagency/jubilee/issues/43
Fixing it though may actually fix the related issue also. Fingers crossed!

Poofjunior, 2020-02-16:
[assembly instructions](https://github.com/machineagency/jubilee/blob/master/tools/jubilee_tools/tool_posts/configurable_tool_post/assembly_instructions/parking_post_assembly_instructions.p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)
[STLs](https://github.com/machineagency/jubilee/tree/master/tools/jubilee_tools/tool_posts/configurable_tool_post/fabrication_exports)

AB Testing this now.

Poofjunior, 2020-02-16:
With new (more rigid) parking post:
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

With old parking post:
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

Poofjunior, 2020-02-16:
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
Welp... that's a major improvement.

The above print was done with the new parking post updated for both extruders on Jubilee V2. (0.2mm layer height, original size.)

Poofjunior, 2020-02-20:
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
I'm marking this solved.

Closed 2020-02-20.

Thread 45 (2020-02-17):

Z Homing switch easily damaged

DanalEstes, 2020-02-17:
Any single event that causes Z to not immediately stop will destroy the switch.  These events may occur during initial commissioning, or during regular operation.

I'm on my 7th replacement Z homing switch

Poofjunior, 2020-02-17:
Yup; I've broken a few myself. Let's start caching ideas here. Here's mine:

I'm really partial to JSteve White's Marionette Probe modification for the Railcore. ([Video](https://www.youtube.com/watch?v=jqDydHZzukI
).) It's retractable and driven by a cable. We could adapt a similar concept inside of the center carriage and tie the probe's retraction cable to the toolchanger Remote Elastic Lock motor. When the tool is unlocked, the probe is exposed. When the tool is locked, the probe is extended.

DanalEstes, 2020-02-17:
I do like the Marionette Probe.  However, if we unlock the tool... well, mine tend to fall off.  Or am I misreading this?

Poofjunior, 2020-02-17:
The Marionette Probe is a cable-driven retractable switch. The idea is that we retract it when tools are locked in the carriage and unretract it when the carriage is bare. That just-so-happens to correspond to  motor movement on the Remote Elastic Lock, so we could attach the cables to the same actuation point.

DanalEstes, 2020-02-17:
Running the Marionette that way would be elegant in an engineering sense.  However, it would rule out probing with a tool mounted.

Poofjunior, 2020-02-17:
Yeah, totally like the appeal, but it may not be necessary or worth doing yet.

You bring up a good point, but it does make me want to ask about conventional use cases. I know z probing with the extruder mounted is how classic 3D printers work, but Jubilee and the E3D Motion System both detach their tools to do the probing. With the capability to remove tools repeatably, is there a reason to still want to probe with the extruder mounted?

### Damage Causes
I have damaged my probe twice, first from scraping it against the bed during toolchanges on the first couple printing layers (fixed by adding a Z hop in the tool change macro) and second from a print fail where the nozzle blobbed up with a goopy mess of PETG that eventually broke off and collided with the Z probe. Can you remember any specific damage causing events?

yvessa, 2020-12-05:
I have just snapped a switch because of a warped layer and eventually, it hit the switch badly.  I'll finish my build and setup it correctly then I might look at it. An idea passing thru my mind, using the twist lock to retract the switch completely while locking the tool and expose it while unlocking the tool.  We could attach a cam or lever arm to the twist lock to do so.  And if moving the switch is not accurate enough, we could drop a guard around the switch using the twist lock while locking a tool. Does it make sense?

javimurcia, 2020-12-08:
Xon 🇦🇺 has reported on discord (https://discord.com/channels/627982902738681876/627988906943578113/785090315346247711) he scraped his Z Switch against the 2 rear retainer screws of the build plate, the ones used as a guide for aligning the removable magnetic plate.

Maybe, we should replace those 2 screws with grub screws so they don't protrude from the print surface.

MichaelPanzer, 2025-02-24:
Hey, Seems like nobody has addressed this in a while. Has anyone considered modifying the carriage to house a bl-touch or something similar?

jackantubis, 2025-02-24:
> Hey, Seems like nobody has addressed this in a while. Has anyone considered modifying the carriage to house a bl-touch or something similar?

Hi, some design add metal pin to avoid killing switch, the metal pin presse on the standard switch and the depth of the pin is set to avoid to kill the switch by too much Z pressure. If you need it I can share the design, check the discord too for this design 👍

MichaelPanzer, 2025-03-17:
It would be very helpful if you could share that deign with me. I already broke one switch and I would like to avoid breaking more.

jackantubis, 2025-03-21:
https://github.com/jackantubis/JUBILEE-Jackantubis-MODS/tree/main/Z%20switch%20mod%20aluminium%20carriage

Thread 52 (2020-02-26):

Toolchanger Lock Actuator Assembly 4 of 15

kelliead, 2020-02-26:
Toolchanger Lock Actuator Assembly, sheet 4 of 15, Fixed Half Pulley with Inserts

Screw is very hard to twist in - make this hole very slightly bigger in the Fixed Half-Pulley With Insert CAD file.

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

Poofjunior, 2020-04-12:
This is now fixed!

Closed 2020-04-12.

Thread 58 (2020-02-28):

Spacer is needed on the inside of the center carriage, around the twist-lock shaft

marioquake, 2020-02-28:
I made a spacer that goes around the twist lock shaft, inside the carriage. it goes between the e-clip and the tool-side, which prevents the twist lock from pulling out from the pulley. It also makes it so i don't have to twist the set screw on the pulley down too far.

if you think about it, the e clip is on the wrong side. its current location prevents the twist lock from going out towards the pulley. But the force is going the other way when you lock onto a tool. the only thing keeping it from slipping out of the pulley is the set screw on the pulley.  this spacer effectively puts the e-clip on both sides inside the center carriage. so it cant slip either direction.

I recommend adding this spacer to your design. It is a simple cylindrical 3d printed spacer, 5.1mm ID, 8mm OD, 27.2mm long.
I ended up filing down the cylinder a tad, and using extra shims to get the fit just right.

Poofjunior, 2020-02-28:
This is a really slick fix to this issue. (Attaching your image from Discord as well.)
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
Overall, this looks like a really elegant way to solve this problem.

For reference, the original intention behind the e-clip was to fix the distance between twist lock head and coupling pins to a specific distance. Your solution finishes the task of more cleanly constraining it axially both travel directions. This change also removes the purpose of the Belleville Disc Spring, since it basically completely takes out any axial play.

I would like to merge this, but I also don't want to merge anything on principle without actually validating that it actually works. @marioquake  would you be willing to run your machine in this state and run a test print that requires a few hundred tool changes? The [Dual Color Moai model](https://www.thingiverse.com/thing:1560492) would be a great place to start.

I would also be happy to pilot this fix on my end also.

devcodeio, 2020-03-03:
Question, you had stated that the disc spring serves to add some compression to the twist lock, and that we actually want a bit of axial movement here.  I was thinking it was akin to the spring and thrust bearing that the e3d lock utilizes, adding some compressive force when locking. An assumption that may be incorrect.

Wouldn't the spacer remove that then?   Or am i just misunderstanding the whats at play here?

Poofjunior, 2020-03-03:
@devcodeio good eye. Depending on how it's put together, this setup could remove the axial compression if we also remove the disc spring.

However, you could totally add the disc spring internally where the new spacer would lie to achieve the same effect.

It's worth testing both with and without the disc spring at this point. (It would be kinda nice to remove it since folks need to buy them in 12-packs.)

Poofjunior, 2020-04-12:
Ok I have removed the Belleville Disc spring and added a spacer on my machine, and this seems to be working.

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

Thanks for the input! This is now live on the master branch.

Closed 2020-04-12.

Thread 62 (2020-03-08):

Add PT1000 to Extruder BOM

HaythamB, 2020-03-08:
Currently the BMG BOM includes a setup for 2x PT100 temperature sensors, plus associated daughter baords.

The newer PT1000 are now available and don't require a daughter board for Duet, so would be a cheaper option to include.

Poofjunior, 2020-03-17:
Whoa--great mod! I will link to this one for the US
https://www.filastruder.com/collections/all-products/products/e3d-pt1000-sensor

Any notes on how the configuration files change?

HaythamB, 2020-03-17:
Haven't tried it myself, but according to [this Duet forum post](https://forum.duet3d.com/topic/9903/pt1000-temps-are-way-off/4?_=1584482030598), its as simple as M305 Px(heater channel) X500 and you're off. Would need someone who's tried this to chime in..

Poofjunior, 2020-03-17:
Okk, since it's optional, I have added it to the BOM. (I also removed the the thermocouple board, which was an extraneous buy from the getgo if you were using thermistors.)

Thanks for the pro-tip!

Closed 2020-03-17.

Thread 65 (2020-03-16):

Acrylic back panel assembly interference

BryanHaven, 2020-03-16:
During assembly it was noted that core x-y stepper motors interfere with the upper outer screws.

It was also noted that the tool locking mechanism must be removed to allow panel to be mounted.

BryanHaven, 2020-03-16:
(https://cdn.discordapp.com/attachments/678103924598898696/688947573020557513/IMG_20200315_231109.jpg)

Poofjunior, 2020-03-17:
Good catch. I moved those, but it looks like I didn't move them far enough.

Poofjunior, 2020-06-29:
The screw location is now fixed.

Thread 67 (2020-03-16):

Mod silicone heater pad to become safer

HaythamB, 2020-03-16:
The standard Keenovo pad wiring is fiberglass sheathing, which tends to quickly wear off from movement and expose the live wires inside. Especially hazardous if we're using an AC pad.

The instructions should reflect replacing the moving components of the heated bed power wires from around the strain relief point to be spliced in with flexible silicone wire, minimum 16AWG /240VAC, 12AWG / 110VAC.

Additionally, consider adding a thermal fuse spliced inline with one of the bed cables, and fastened to the bottom of the heater pad using high-temperature silicone sealant (or equivalent high temp adhesive) to also enhance safety in case of an SSR failure or other AC electrical mishap.  Here's one that I used for my heated bed (you'll need to choose one based on the cutoff temperature for your own build plate). [Thermal fuse for heated bed](https://uk.rs-online.com/web/p/thermal-fuses/7976052/?sra=pstk)

Poofjunior, 2020-03-17:
The current instructions have you sheath the two bed leads together into a nylon sleeve. In that configuration, the leads move as a pair such that they do not abrade each other and they are also protected from abrading anything external.

Additionally, while this may seem unintuitive, the adhesive silicone block on the edge of the bed already serves as a form of strain relief for the two bed leads. What do you envision as an improvement?

Finally, that thermal cutoff is a great safety mod! I'm looking into an easier way to do this in the back of the machine with a bolt-on solution that doesn't require silicone.

HaythamB, 2020-03-17:
I was thinking along the lines of a drag chain, which could possibly be mounted to the bottom of the bed or even screwed on to the Z-axis mount in the rear. On my build the bed is a non-Jubilee subframe where I've attached a drag chain using t-nuts to the rear extrusion.

So its either a couple of blind taps in the bed, or an attachment onto the Z-axis 3D printed part, possibly at the angled face. It could be either 2xM3 or 1xM3, depending on the drag chain used.

Poofjunior, 2020-03-17:
Gotcha. I'd totally take inspiration from pics if you're willing to showcase a couple. For the Z axis, the clearance is pretty tight. One thing to keep in mind is that all fixed or moving components on the bed need to be at the bed plate level or below or they risk snapping the Z axis limit switch.

For thermal cutoff, instead of glue, I'm looking for something to clasp the fuse that you can just bolt-on, kinda like this:
https://www.digikey.com/product-detail/en/keystone-electronics/8140/36-8140-ND/303983

Poofjunior, 2020-03-17:
Actually, this half-cable clamp
https://www.newark.com/ettinger/14-42-341/half-cable-clamp-steel-natural/dp/58Y8078
might work really well with this fuse
https://www.digikey.com/product-detail/en/cantherm/SDF-DF119S/317-1132-ND/1014761

HaythamB, 2020-03-18:
That does look like a great solution, and it comes in a selection of temperatures that people could choose to suit their liking. Only question that remains is if it will remain tight to the bed after repeated movements. Looking at the half clamp tells me it would for 90% of the cases. But I'll stick with sealant to be absolutely sure.

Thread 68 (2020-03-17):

Add additional clearance on motor mounts.

SteveJWallace, 2020-03-17:
Additional clearance should be implemented on the slot that allows the motors to slide along the plate. It was necessary to add 0.3mm to each one for the motors to fit in place snugly.  The parts were printed with the recommended settings in PETG.

[Motor Corner Brackets.zip](https://github.com/machineagency/jubilee/files/4341282/Motor.Corner.Brackets.zip)

Poofjunior, 2020-04-12:
This is now fixed in master.

Closed 2020-04-12.

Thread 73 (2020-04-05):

BOM Error, M2 Buttonhead screw, 8mm long missing

SteveJWallace, 2020-04-05:
The BOM is missing the M2 Buttonhead screw, 8mm long that was mentioned in the instructions for the toolchanger lock assembly on sheet 7 of 15.

Poofjunior, 2020-04-23:
Oh, these are in the McMaster-Carr section, since they need to be buttonhead, which BoltDepot doesn't have.

Alas, you need to buy a 100-pack for only two screws, but def will take suggestions for other places.

Poofjunior, 2020-04-23:
spoke too soon!
https://www.aliexpress.com/item/33007621009.html

VinnyCordeiro, 2020-04-23:
There's this link for titanium-plated screws that can be bought down to only 5 units, if you don't mind golden screws: https://www.aliexpress.com/item/4000352613356.html

Closed 2020-04-23.

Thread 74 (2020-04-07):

Twist in the CoreXY frame

erikmcclain, 2020-04-07:
Depending on how the machine is assembled it is possible to end up with a twist in the Corexy.

If there is twist maybe recommendation on how to solve it

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

by Loosening, reclamping the high corners then tightening them back down

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

nexx, 2020-05-29:
@erikmcclain. I'm sorry to intrude, as my enquiry doesn't relate to the Jubilee, but I'm yet to find another person talking about this kind of twist in a CoreXY frame combined with a 3 point kinematic bed. I've been building a RatRig V-Core Pro and adapted it to feature a kinematic bed with 3 independent Z motors. I have exactly this issue where the two free corners have a difference from one side to the other of nearly 1mm despite the 3 Z points being at 0. I know it is not the bed itself, it's 6mm of tooling plate which I know is almost perfectly flat (and I've tried 2 separate sheets), but I've been unable to correct the tilt.

I've checked, measured, double-checked and re-built the frame multiple times now and the results are always the same. I would really appreciate any thoughts you may have on what to try as I'm on the verge of throwing the frame out of the window :P

erikmcclain, 2020-05-29:
Have you joined the jubilee discord?  It would be a good place to have a general discussion.  I would like to see some screen shots of what you have going on.

That said what I did is put a 12 by 12 polished granit tile on my bed and mesh off of that.  That gave be a very flat surface to start with.  And proved to me that it was a twist in the motion system.   Next I measured the diagonals and I noticed that the front for of the machine had a very slight lean to it.  So I pulled the frame until the I measured identical diagonals.

That took about 1/3 of my twist out.  Next I loosened the low corner indicated by the mesh and the one diagonally across, put a clamp being enough to clamp the top and bottom frames together and tighted everything back up.  That took out about half of the remaining twist.

Lastly I let the bed heat up for a out 5 min or so with the regular bed surface on.  I homed trammed and meshed.  After that mesh with everything hot for some reason most of the last bit of twist was gone.

nexx, 2020-05-30:
> Have you joined the jubilee discord? It would be a good place to have a general discussion. I would like to see some screen shots of what you have going on.

I don't really use discord I'm afraid.

> That said what I did is put a 12 by 12 polished granit tile on my bed and mesh off of that. That gave be a very flat surface to start with. And proved to me that it was a twist in the motion system. Next I measured the diagonals and I noticed that the front for of the machine had a very slight lean to it. So I pulled the frame until the I measured identical diagonals.
>
> That took about 1/3 of my twist out. Next I loosened the low corner indicated by the mesh and the one diagonally across, put a clamp being enough to clamp the top and bottom frames together and tighted everything back up. That took out about half of the remaining twist.

My latest attempt involved completely rebuilding the frame and using a spare extrusion with 3D printed parts on it as a calibration device. As near as I can tell, every pat of the frame is identically measured and square. That's what makes this so frustrating. I'm also certain that the upright extrusions for the 3 Z axes are both square and true. All the rails were mounted to the extrusions with a set of 3D printed spacers to ensure they're centred.

> Lastly I let the bed heat up for a out 5 min or so with the regular bed surface on. I homed trammed and meshed. After that mesh with everything hot for some reason most of the last bit of twist was gone.

I've not made it that far. I've been doing all measurements with a dial indicator mounted to the X axis. If it's any aid in troubleshooting, I've found that lowering the front right Z point will cause the rear to level out left to right, but then the front is obviously no longer level.

I've also tried two separate tooling plates, both show the same error, so I'm certain they're flat within 0.1mm or less.

Here's a render of the build showing the layout of the axes:
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

Prexsys-Beach, 2020-05-30:
Not to be impolite, but perhaps you guys could take this somewhere else :)
I get enough notices about Jubilee stuff :) Good articles on machine
alignment are numerous.  Thank you!

On Sat, May 30, 2020 at 12:37 PM Simon Davie <notifications@github.com>
wrote:

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

nexx, 2020-05-30:
Apologies @Prexsys-Beach. I won't bother you guys further with unrelated matters. Thank you anyway.

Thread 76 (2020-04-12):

Z-Axis - improved genericism across motor brands

BryanHaven, 2020-04-12:
Many motors have varying shaft lengths - topping out at 25mm. Adding to motor plate thickness and z-thrust spacer should resolve.

Poofjunior, 2020-04-29:
@BryanHaven just curious: in your implementation, how much space did you put between the motor and the Z plate? What's your spacer length?

Poofjunior, 2020-05-30:
This has been bumped down in 2.1.0 such that the leadscrew need only be installed 7-to-9mm, rather than bottom out in the plastic piece.

Poofjunior, 2020-05-30:
Oh, and motors of 24 and 25mm shafts should work in this section as well!

Closed 2020-05-30.

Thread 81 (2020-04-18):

Questions about purpose of shims and shoulder screws in pulley assemblies

crteensy, 2020-04-18:
I have questions regarding the shims and shoulder screws in the pulley assemblies.

**Shims:**
The shims are installed between idler pulleys and printed parts, or between pulleys and plain washers. However, in the "Left Motor Pulley Assembly", there's no shim between the pulley and the "Pulley reinforcement plate for motor". Why?

Also, the standard shims I have looked at do have an outer diameter that is just as large as that of many ball bearing used in idler pulleys. Wouldn't they rub against the bearing's rotating outer ring?

Could 3d printed washers with the right thickness be used instead? Those could also solve the diameter issue - if there is any.

**Shoulder screws:**
I do understand that shoulder screws provide for a more exact centering of the installed parts, and a better surface of ball bearings to press against. They also screw directly into inserts, so that the screw's shaft can press against the insert which results in a correct 90° angle and good transmission of forces without any wiggle. Is that the idea why they're used?

However, shoulder screws are expensive - could normal screws be used and what changes to the design would be necessary?

crteensy, 2020-04-18:
An idea for a replacement: instead of an M4 shoulder screw (25 mm shaft with 5 mm diameter), could we use an M4x30 screw and a piece of 5x0.5 mm pipe (brass would be easy)?

Poofjunior, 2020-04-19:
These are some great observations/questions.

**Shim**
You're right about the shim outer diameter being a bit a bit wider than the outer diameter of the pulley bearing, which would cause rubbing on sliding surfaces. In practice, in this setup, this is ok because the rubbing is happening on a smoother surface (the face of the shim) rather than the opposite pulley faces. That said, a smaller shim would be ideal here to act as a true spacer with no rubbing surfaces, so I spec'ed an 8mm OD shim and added it to the BOM yesterday. (It's also cheaper!)

As for why there's no shim on the top of the shoulder screw stack in the motor plates, that's because the original motor reinforcement plates were made from Delrin, a very slippy material to begin with. Since the current motor reinforcement plates are printed, it's worth adding them back.

**Shoulder Screws**
In a nutshell, shoulder screws are behaving like shafts in all cases here. True, the outermost diameter of an M5 screw is close to 5mm, but it's not quite close enough (4.826 to 4.976). As a result, the pulley would move around loosely in the shaft. While this probably wouldn't do too much to printer tolerances, it probably would cause a lot of extra vibration and possibly unscrew the screw from its hole without some threadlock. Shoulder screws are dimensioned such that bearings can slide onto the shaft smoothly with little room for any wiggle. One more thing: the bottom surface of the shoulder screw (as you mention) forms a nice contact point with the surface of the connecting plate. Tightening the shoulder screw creates a normal force (a preload) between screw and plate which actually prevents it from unscrewing itself during normal operation.

All-in-all, if you're looking to save money,
* swapping out the electronics for a cheaper controller board
* using unbranded linear rails instead of LDO or Hiwin brand rails
* using generic pulleys instead of Gates brand Idler pulleys
all might be other places to start that wont really sacrifice machine performance.

I hope this helps!

BTW, I'll leave this issue open until I add back the 0.2mm shim on the tops of all shoulder screw stacks.

crteensy, 2020-04-19:
Indeed there's more money to be saved in the parts you mentioned (electronics, rails, pulleys, maybe others too).

I'll have a look around and see what kind of screws I can obtain easily and at reasonable cost. It's not equally easy everywhere.

Poofjunior, 2020-04-29:
Getting back to this a bit late, but you may have some great luck with stainless steel shoulder screws on Aliexpress. I've not tried sourcing shoulder screws from them, but I did notice a good selection.

crteensy, 2020-04-29:
No problem - but the prices are still quite high. Actually the same as for screws sourced locally in DE.

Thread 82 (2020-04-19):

Feet are too short, screw clearances are too tight

BryanHaven, 2020-04-19:
The budget feet are too short to allow heat sinks on a Z-axis stepper motor with a 25mm shaft. Recommend adding at least 10mm.

The mounting screw counterbore clearance is too small for the designated M5 x 10mm long screws.

Poofjunior, 2020-04-21:
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
Adding image from Discord for reference.

Just curious, how short is too short? The ones in the BOM are 48mm long. That puts 12mm between the bottom of the motor and the bottom of the foot. I agree that that's not much room for a heatsink, but adding 10mm seems a bit much over, let's say 5mm.

Also: will get the buttonhead screw counterbore hole updated in 2.0.3.

Poofjunior, 2020-06-29:
The Zaxis motors were bumped downwards in 2.1.0, but the feet have now been made taller in 2.1.1.

The total offset between the lowest part of the motor and the floor is now 15mm, which should be plenty of clearance for a heatsink.

Closed 2020-06-29.

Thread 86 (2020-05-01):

Missing shoulder bolt listed in

Prexsys-Beach, 2020-05-01:
The new 25mm shoulder bolts needed in 041_Aluminium_Crossbar_Assembly_Instructions  / Sht 5 of 8 (04/12/2020) are missing from the BOM. The existing BOM lists 90278A374 which is M4 Shoulder Screw, 20mm-l, 5mm-d which is for use with the Delrin bracket.

McMaster Carr 90278A375 is the 25mm version of the same bolt.

Poofjunior, 2020-05-05:
Aye; aluminum corner plates are currently "upgrades" in 2.0.2, so the extra parts that you'll need to buy are listed on Mandala Rose Works' webpage for now, but 25mm shoulder screws should now be the standard.

I think* this is resolved as of now?
If not, you could be looking at an out of date copy of the bom (perhaps the UK bom?) Here's the main one.
https://docs.google.com/spreadsheets/d/1pRzBQxVzL9c4T9b1RrKvSjlSwJJhJ7NcbSV6iJUv0X0/edit#gid=0

Let me know if this is still an issue.

Poofjunior, 2020-05-29:
This should be a non-issue now that 2.1.0 is released.

Prexsys-Beach, 2020-05-29:
Was not looking at UK version

On Tue, May 5, 2020 at 3:07 PM Joshua Vasquez <notifications@github.com>
wrote:

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

Closed 2020-05-29.

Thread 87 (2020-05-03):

Spring length(s) required missing from BOM

hexblot, 2020-05-03:
Hello,
I am in the process of sourcing the various items in the BOM from the EU and have the following requirement for clarification:

In the given Google Sheet BOM, tab "Frame Shopping List", row 8, for "Sping Guide 0.088-in outer-dia", there are no length dimensions listed, making the pre-cut external link (lukeslab.online) the authoritative source for the needed lengths ( 1x 600mm + 1x106.5mm).

1) Kindly confirm these are correct (and only!) lengths required
2) Kindly update the BOM to reflect these values instead of relying on an external source to provide the info.

Thank you in advance!

Poofjunior, 2020-05-05:
Yes, these are correct! Their lengths are now listed in the BOM as well. Thanks for the catch!

Closed 2020-05-05.

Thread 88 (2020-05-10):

X Axis Home Offset is slightly off.

Poofjunior, 2020-05-10:
The default config file lists an offset of -11.5mm.
https://github.com/machineagency/jubilee/blob/master/software/duet_config_files/duet2/sys/config.g#L69
This should be closer to 13.5-to-14mm. (Something between versions was either never correct, or may have changed as printed parts changed.)

Poofjunior, 2020-05-11:
From the CAD model, this should be 13.75mm. But since the switch operating position has a tolerance, this location could vary by +/- 0.2mm.

Poofjunior, 2020-08-17:
This is now fixed in master.

Closed 2020-08-17.

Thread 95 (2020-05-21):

Carriage Center Plate screws should have inserts.

SteveJWallace, 2020-05-21:
I would suggest either heat set inserts should be added or have the bolts go through the carriage completely as they are very likely to strip out when tightened and make disassembly difficult. It also allows for better compression.

Poofjunior, 2020-05-23:
Aye; this will be out in the next release. The carriage front and back plates do need to be occasionally removed for servicing, so this is a good way to prevent folks from stripping screws.

Poofjunior, 2020-06-23:
This is done :)

Closed 2020-06-23.

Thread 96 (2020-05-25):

Default Tool Wiring, numbers don't add up?

quadrupedal, 2020-05-25:
The Default Tool Wiring for Duet2 (https://github.com/machineagency/jubilee/blob/master/tools/jubilee_tools/tools/extruders/direct_drive_bondtech_groovemount_extruder/assembly_instructions/wiring/duet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) gives a suggested sleeved length of 1650mm with  exposed lengths of 100mm and 200mm for each end, which gives a total length of 1950mm, which doesn't match the given suggested total harness length of 1800mm, so it is not clear how these numbers relate to each other.

Poofjunior, 2020-05-26:
Thanks for the heads up. Just fixed this. It also looks like these should be about 2400mm, based on recently wiring a tool.

Closed 2020-05-26.

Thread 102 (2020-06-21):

G10 / Non-standard

arthurwolf, 2020-06-21:
Hello.

This page : https://jubilee3d.com/index.php?title=TAMV says you are using G10 for a completely out of specs usage. Please please don't! Standards matter, in particular for folks trying to make systems that can run both 3D printer and CNC mill gcode on the same system ( I'm from the smoothieware.org project, which enables this )

We already have a huge issue with the fact that Reprap started using G10 for extruder retract, when it should in fact be a tool to set WCS coordinates ( see the NIST gcode spec ). Now the same Gcode means two completely different things, and we have to jump through hoops all the time thanks to that.

The fact Reprap didn't respect the NIST standards has caused us massive amounts of headache over the years. Please, I beg of you, don't make that issue worse.

You should be able to use G54/G53, and the *normal* version of G10 to do what you want. Please don't create an *additional* out-of-standard G10 use.
If you have a hard time understanding how to use the proper Gcodes here, please tell me and I'll help as much as I can. wolf.arthur@gmail.com

Cheers!

http://smoothieware.org/g10
https://reprap.org/wiki/G-code#G10:_Retract
https://linuxcnc.org/docs/html/gcode.html
https://linuxcnc.org/docs/html/gcode/g-code.html#gcode:g10-l1

HaythamB, 2020-06-21:
While that's a very valid input and useful suggestion, it's not something inherent to the Jubilee/TAMV implementation. It's just following the convention from RRF.

Maybe a post on the Duet forums would be in order?

arthurwolf, 2020-06-21:
Thanks, emailed David, hopefully he comes here and gives some more info.

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

--

勇気とユーモア

Poofjunior, 2020-06-21:
Oof; it sounds like non-standard use of Gcode commands has caused you a huge development headache. Happy to switch over to conventions that are according to spec if it's possible with the Duet board we're currently working with.

Looking at the Duet [G10 documentation](https://duet3d.dozuki.com/Wiki/Gcode#Section_G10_Tool_Offset_and_Temperature_Setting), it looks like they support a G10 command _with_ and _without_ an L parameter. If the L parameter is omitted, it assumes L=1, which would be a tool table entry.

Can you double-check me here? It looks like, according the LinuxCNC doc, tool offsets can be defined with [G10 L=1](https://linuxcnc.org/docs/html/gcode/g-code.html#gcode:g10-l1), but the arguments are limited to tool radius and a few other lathe-only parameters. On a non-spindle machine with multiple tools like a toolchanging printer, a "radius" argument doesn't make sense, but _x_, _y_, and _z_ arguments do make sense.

You mentioned using G53 and G54 for defining tool offsets. Are you suggesting defining one work-place coordinate system per tool? If that's the case, wouldn't we restrict total tool count to 9 tools? If not, can you clarify how we'd go about setting XYZ tool offsets per tool in a way that follows the spec.

Thanks again for chiming in!

arthurwolf, 2020-06-21:
http://smoothieware.org/g10
http://smoothieware.org/g54

More generally :
* http://smoothieware.org/supported-g-codes
* https://linuxcnc.org/docs/html/gcode/coordinates.html
* http://linuxcnc.org/docs/html/gcode/g-code.html#gcode:g10-l2

> Are you suggesting defining one workspace coordinate system per tool?

No, just set the offset for the current workspace ( in XYZ, there is no
tool radius involved here ).

On Sun, Jun 21, 2020 at 8:09 PM Joshua Vasquez <notifications@github.com>
wrote:

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

--

勇気とユーモア

Poofjunior, 2020-06-21:
Right, but in a multitool setup, we'd likely need unique offsets per tool. Wouldn't that require a custom work offset per tool? i.e: G54 for tool 1, G55 for tool 2, etc. How would we accomplish this with a single workspace coordinate system?

Unless I'm totally misreading something. Are you actually ok with this syntax:
```
G10 L1 P<tool number> X<value> Y<value> Z<value>
```
but not this syntax:
```
G10 P<tool number> X<value> Y<value> Z<value>
```
?
If that's the case, then this something we can just edit in the wiki, as it is in-line with the current duet implementation. If not, can you be a bit more specific about what's incorrect about what's written in the TAMV page regarding G10? If it ends up being a wiki issue, we can fix that. If it's a Duet GCode implementation, then I would gladly vouch for you if you post in the Duet forums. I'd much rather we push for standards rather than reinvent conveniences for ourselves.

arthurwolf, 2020-06-21:
On Sun, Jun 21, 2020 at 9:53 PM Joshua Vasquez <notifications@github.com>
wrote:

> Right, but in a multitool setup, we'd likely need unique offsets per tool.
>
You'd store those inside the host program's config, and use it to adjust
the offset of a single WCS when a tool is changed.
Doing otherwise wouldn't match what those Gcodes are for.

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
Stay in G54, and use G10 L* to modify the offsets for that WCS when
changing tools.

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
Yes, that's standard.

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
And that one isn't standard.

It's all documented:
https://linuxcnc.org/docs/html/gcode/g-code.html#gcode:g10-l2
https://linuxcnc.org/docs/html/gcode/g-code.html#gcode:g10-l20

You stay in G54, and use those to change the offsets whenever you need to (
here when changing a tool ).
This is the correct/standard way of handling this.

Does that clarify the situation?

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

--

勇気とユーモア

Poofjunior, 2020-06-21:
Ok,
```
G10 L1 P<tool number> X<value> Y<value> Z<value>
```
is supported syntax in the Duet implementation. Happy to be more explicit in the configs and wiki by referring to them as such.

Ok, next question:

> You stay in G54, and use those to change the offsets whenever you need to (
here when changing a tool

So each time you invoke a tool change, are you saying, you'd follow up with
```G10 L1 P<tool index> X<value> Y<value> Z<value>```? Doesn't that go against the notion of defining these all in advance with a tool table?

dc42, 2020-06-22:
The way RRF behaves in response to a G10 command is:

- G10 with a P parameter but no L parameter sets tool offsets and/or temperatures for the tool specified by the P parameter. This was defined behaviour of RRF before I became involved with it.
- G10 L1 behaves the same as above. This is compatible with LinuxCNC, apart from the option in RRF to set tool temperatures
- G10 L2 sets workplace coordinate offsets in accordance with the NIST GCode standard.
- G10 L20 sets workplace coordinate offsets based on the current tool position. We implemented this version of G10 for compatibility with LinuxCNC.
- G10 with no parameters is a firmware retraction command, compatible with Marlin, Repetier etc.

When you do a tool change, RRF loads the new tool offsets automatically. So no need to follow a tool change with G1 L1 commands.

HTH David

Poofjunior, 2020-07-19:
I have adjusted the docs to suggest more NIST-like usage in the [TAMV docs](https://jubilee3d.com/index.php?title=TAMV#Overview). Thanks all for bringing all this up.

Closed 2020-07-19.

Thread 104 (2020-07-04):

Lock actuator motor plate STL not updated for LDO diameter

coldelectrons, 2020-07-04:
Somehow, the STL was 'updated' at the same time as the motor base, but the diameter still corresponds to the StepperOnline motor. The corresponding part in the jubilee.STEP file is correct, however.

This is in the latest commit, 76700425b644e68d5f71041afc3d75ebb93b6ec9

Poofjunior, 2020-07-04:
Really good catch! Thanks for bringing this up! This should be fixed in this commit
https://github.com/machineagency/jubilee/commit/c35194454748a60f64e4b1f1ce74d91bc4b35f9a?short_path=d27935d

(Checked against Github's nice STL diff rendering feature)

Closed 2020-07-19.

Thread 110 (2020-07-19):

Aluminum Frame not not guaranteed to be electrically connected.

ljones-adaptive, 2020-07-19:
As a user, I would like from an electrical safety point of view to be able to ground the entire frame of the Jubilee 3D printer.

I would be expecting that the tnuts and the corner set screws from the corner brackets, used to assemble the frame, would have suffient bite into the aluminium 2020 extrusion so as to make a complete electrical connection. Thus, allowing the complete frame to be grounded.

The Problem:
I have found on the hidden corner brackets I sourced from China the set screws have a flat bottom and so do not bite.
This means only small portions of my frame are actually connected together.

My solution:
To solve this problem use a continuity tester to inspect the connection between individual 2020 frame extrusions and any found to be non conducting change the set screws for ones with a point until the required connectivity is obtained.

Poofjunior, 2020-07-23:
This is a great point. Just curious: are you using anodized extrusions or unanodized extrusions?

Either way, I think it makes sense to put the builder in a situation where something as simple as a color change doesn't make some machines safer than others. We should test conical or knurled set screws to see if they have enough "bite," and then add them to the BOM.

Thanks for bringing this up!

ljones-adaptive, 2020-07-23:
If I test connectivity using a continuity tester, then I get continuity between the raw ends of the extrusion where a saw has made a cut.
I am unsure what the finish is and can't find where I sourced them from.
If I test conductivity between one of the ends where the cuts are made and any point down the length of the extrusion then I do not get connectivity.
I have solved the problem by using conical pointed set screws for the hidden corner joints.. These bite into the extrusion and make contact. As I change out the set screws, from flat to pointed, I can follow the continuity around the frame until all the extrusions are connected.

So, adding a step to "check continuity" into the bed assembly intructions will probably surfice to increase saftey.

andmiller, 2020-08-12:
The inside brackets here: https://www.amazon.com/s?k=b07vq84gwv&ref=nb_sb_noss looks like it comes with conical set screws, I'll update when I receive them.

andmiller, 2020-08-18:
So the brackets I linked above do indeed come with pointed fasteners and do reliably (from my limited testing) conduct even when only moderately tightened. I have tested with 4 lengths of extrusion that are not touching, but only connected by the brackets and fasteners and get good continuity from the first to the fourth.

Poofjunior, 2020-08-18:
Thanks for checking and following up!
So far, I've listed cup point set screws in the BOM as optional replacements for the ones that come with the L brackets. My hope is that these should cut through the anodization without needing to check, but this is untested.

Big picture here. Long term, my intent is that "blindly" ordering the listed parts in the BOM produces a functional safe machine without the assembler needing to know too much about how certain things work (unless they want to go deeper). With that said, I'm hoping I can add a note about continuity checks *only if you ordered different L brackets.*

Poofjunior, 2021-03-16:
Ok, cup point set screws are now (1) noted in the BOM, (2) mentioned in the [L-Bracket Assembly](https://github.com/machineagency/jubilee/blob/master/frame/assembly_instructions/frame/inside_corner_bracket_prep.pdf), and (3) included in Filastruder's fastener kit by default. (Filastruder also removes the flat-point set screws from the L-Bracket bags.)

Cone point are also listed as an option in the instructions too.

I think it's safe to close this one now. Thanks for the sanity checks during your assembly process @andmiller and the heads-up from the default included screws @ljones-adaptive !

Closed 2021-03-16.

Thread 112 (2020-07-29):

Misconfigured System Breaks X Axis Limit Switch

Poofjunior, 2020-07-29:
If the machine is not responding to endstops, the machine can damage the X limit switch while homing as it continues to travel into the switch, crushing it.

It would make sense to create a situation where, even if the switch doesn't trigger, the machine hard-stops, rather than causing damage to itself that requires the user to service it. (The Y Axis is like this. Rather than break the switch, it hard-stops into the frame.)

coldelectrons, 2020-10-23:
I suggest a modification of CBP-05: extend the plastic past the switch by 3.0 to 3.2 mm. Based on my digital calipers and one of those switches, that is how far the plunger still extends when triggered. The switch itself can remain in the exact same position.
I myself have now clobbered two of those switches getting my Jubilee moving for the first time.

Poofjunior, 2020-10-24:
Thanks for the rec @coldelectrons ! This is one possible solution. We'll have to check to see if we need to modify the corresponding tab where the switch triggers, so there's a low-stress surface to act as a hard-stop.

Poofjunior, 2021-06-03:
Ok, here is an in-progress solution in related issue: https://github.com/machineagency/jubilee/issues/180

Poofjunior, 2021-06-03:
Ok, instructions are updated.
This part is now in the print list:
https://github.com/machineagency/jubilee/blob/main/frame/fabrication_exports/3d_printed_parts/frame/x_axis_hard_stop.STL

And I think we're a lot better now than where we were!

Closed 2021-06-03.

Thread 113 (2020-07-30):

Printed Belt Clamps Could be Stronger

Poofjunior, 2020-07-30:
Some folks' belt clamps are snapping during normal use.

There are a couple options:
1. Add a torque spec for tightening them
2. Make the part stronger

I'll opt for Option 2.

Poofjunior, 2020-10-29:
This was completed in 2.1.2

Closed 2020-10-29.

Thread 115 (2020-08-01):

47mm parking post has wrong dowel centers

ljones-adaptive, 2020-08-01:
Upon checking the dowel centers for the Pen holder it looks like the 47mm parking post has dowel centers that are to far apart.

I measured the centers of the dowels for the 47mm parking post which are actually 55mm and the centers of the location circles for the passive pen holder which is 47mm.

So, at some time it looks like the 47mm tool holder got stretched to 55mm dowel centers.

Poofjunior, 2020-08-02:
Yeah; I thought I fixed this a while ago. It turns out I was driving the model with the wrong parameter.

The revision number is ticked (so we don't confuse these parts) and the number is now fixed.
* the XX values in PPBXX-04 and THXX-04 should now reflect the center to center dowel pin distance.
* PPB47-04 and TH47-04 re-exported
* PP55 is now created, which is the corrected default tool parking post
*  instructions for the tool holder are now updated
* wiki is up to date with links

Closed 2020-08-02.

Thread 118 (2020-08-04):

M5x10x0.2mm shims from McMaster might not fit on spindle.

JacobRoth, 2020-08-04:
M5x10x0.2 shims from McMaster-Carr (part number 98089A246) have an ID tolerance that allows them to be as small as 4.7mm, which can make them too tight to fit on the twist lock spindle. In my case none of an entire 25 pack of these shims could fit onto my spindle.

Poofjunior, 2020-09-05:
Ok, these are removed from the BOM as alternates to the Aliexpress ones. Thanks a bunch for the heads-up.

Closed 2020-09-05.

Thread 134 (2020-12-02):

Toolchanger Remote Elastic Lock Assembly references outdated version of part

ioben, 2020-12-02:
The assembly instruction PDF for the [Toolchanger Remote Elastic Lock Assembly](https://github.com/machineagency/jubilee/blob/master/frame/assembly_instructions/toolchanger_mechanism/toolchanger_lock_assembly_instructions.pdf) currently references part CPL-01 on pages 15-17. The next set of instructions in [Toolchanger Carriage Assembly](https://github.com/machineagency/jubilee/blob/master/frame/assembly_instructions/toolchanger_mechanism/toolchanger_carriage_assembly_instructions_draft.pdf) references CPL-02. This disparity initially led me to believe they were two different parts.

Simple fix, but I think it'd help clarity between these two steps quite a bit.

Poofjunior, 2020-12-02:
Aye; that's definitely an issue. I'll have that fixed up for the next release. Thanks for writing this in!

Closed 2020-12-03.

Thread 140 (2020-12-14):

Adapting Jubilee to 3030 extrusions / MGN-xx-H carriages

mhipszki, 2020-12-14:
So I've got access to 3030 extrusions and `MGN-xx-H` rails and I'd like to adapt the designed parts to them.

I noticed that the Jubilee CAD drawings are beautifully organised under the `frame/cads/Solidworks` folder and wonder if it'd be possible to modify or contribute to those parts with a CAD program other than Solidworks?

Unfortunately I don't have access to Solidworks neither I could run it on my Mac. However I noticed I could use the exported STEP file and modify the 3D printable parts for my Jubilee, but then was also thinking there could be other people already having access to these components e.g. they'd like to modify their HEVO, reusing its parts... so might as well publish it for them?

I'm aware though that supporting a 3030 frame would result in duplicate work when it comes to design improvements involving changes in 3D printed / machined parts etc. but maybe it's something worth discussing 🙂

Poofjunior, 2020-12-14:
Yeah; one way to make progress on a 3030 frame would be to start from a Fork of the project and then develop your changes such that they stay in line with the folder structure of the project. You could make a new folder in frame/cads. And if your Fork is public, then folks can use your files as-is, even if you don't have instructions for them or a complete BOM. From here; merging would be a matter of simply merging in your new folders/files.

For now, i think STEP is an acceptable file format if you want to save CAD files that way. Big picture, a competitive, accessible CAD platform is something we could all benefit from, but we just have to do our best for now.

I admit that the bar is high for frame changes. Not because I'm emotionally tied to the design, but because it's tied to a BOM and assembly instructions that make it easier to consistently reproduce from various folks. Having one design also makes it easier for folks to debug each other's setups via Discord. Getting a substantial frame change merged in would probably need to come with instructions and a BOM of some sort so that we could help folks build it to the same level of granularity as they can with the original.

One philosophical question that's been on my mind is: *if the frame is different, is it still Jubilee?* I don't really have a hard answer yet, but I'm leaning towards no. This is because a different frame will have different properties that make it harder to tap into community knowledge to help with bringup/debugging issues that arise.

All that said, I don't want to discourage you from exloring this--you totally should! One thing we can do is, as you make progress and get it online, we can link to it in the wiki. Right now we have a [Community Mods](https://jubilee3d.com/index.php?title=Community_Mods) page, which is like a catch-all for tweaks that people have made. It would be great to develop this more so that other more mature designs get their own page/pages on the wiki to help guide folks who want to explore making changes. It'd give them a sense of what works and what has been done before.

Let me know what you think, and feel free to chime in on Discord too.

mhipszki, 2020-12-18:
Thanks @Poofjunior for being open and kindly sharing your thoughts!

I'm happy to fork the project and work out the changes on the STEP file, however you are absolutely right in that changing the frame would have a knock on effect on most parts and eventually on the BOM and the instructions. Initially when I was thinking how it could be done I didn't take that into consideration.

I totally agree with all that's said and that the intention to keep a single, reproducible and "evolving" version of Jubilee is a very important aspect of a project like this. Still, I'm keen to explore the "3030 frame" route and am willing to spend time on working out the details. I guess the other option would be to just toss the parts I've already got in the drawer and buy all that prescribed in the Jubilee BOM but that would be less fun! 😄

On the philosophical level regarding the naming and relationship, I also understand your thinking and even if I worked out a solution for the public using a 3030 frame I wouldn't be sure myself if it's still a "Jubilee" or not but I'm happy to rely on your recommendation. Let's cross that bridge when we get there!

The plan is to spend time on this project during the coming holidays, so let's see how far I can get. I've joined Discord already and will get in touch there.

Regarding the `competitive, accessible CAD platform`, what do you have in mind?

Poofjunior, 2021-03-16:
Whoop--I'm coming at this pretty late. I'll pop in my last reply, and then we can continue the chat on Discord if you like.

As far as an accessible cad package goes, I think FreeCAD and Alibre are both worth exploring. FreeCAD is open source; Alibre is a one-time purchase (with a significantly cheaper annual upgrade purchase.) Both have some sort of "Assembly" and "dimensioned drawing" application, which something like Jubilee uses heavily to manage the model's complexity and make instructions. As far as what to pursue, I'd be open to what folks think about either!

Closed 2021-03-16.

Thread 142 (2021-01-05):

Back Bed Motor Should have 12mm screws

Poofjunior, 2021-01-05:
Pic says it all.
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

We need to track down if this affects the BOM also.

Poofjunior, 2021-01-31:
This should now be fixed in the main branch.

Closed 2021-01-31.

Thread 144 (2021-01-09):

Duet2/RRF3 Bed.g has inverted probing sequence regarding config.g Z drive declaration

FL-CDF, 2021-01-09:
I had issue with the 3 point bed leveling (see discord troubleshooting chanel), putting the same sequence as config.g solved my issue (Front left then Front right then Back)

There is the bed.g code corrected:
M561 ; Disable any Mesh Bed Compensation
G30 P0 X295 Y295 Z-99999      ; probe near front left leadscrew
G30 P2 X5 Y295 Z-99999	  ; probe near front right leadscrew
G30 P1 X152.5 Y5 Z-99999 S3  ; probe near back leadscrew and calibrate 3 motors
G29 S1   ; Enable Mesh Bed Compensation

Poofjunior, 2021-01-09:
Thanks for the heads-up. I'll have a look on this vs what's on the stock setup.

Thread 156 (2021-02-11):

rrf3 home macro fix

grzesiekn, 2021-02-11:
When I try to home X axes first I getting message "G28 may not be used within a homing file". Any solution for this - except: home U,Y first.
I think You can replace **G28** with **M98 P"home?.g"**
Affected files homex.g and homez.g

It will be good idea to add an IF before Rapid moves in tfree, tpost, tpre files
if move.axes[1].userPosition >= 305
  G0 Y305 F20000             ; Rapid to safe y position

It looks like in the file confg.g M950 commands is missing that defines heater fans:
M950 F1 C"fan1"                         ; Fan 1, heater cooler fan on Tool 0
M950 F3 C"fan3"                         ; Fan 2, heater cooler fan on Tool 1

Poofjunior, 2021-03-18:
Ok; I think this actually got fixed on Feb 11.
https://github.com/machineagency/jubilee/commit/dc2cee648ddfca3b81d67750f0e6f9638a68ccb1

If there's still an issue, fee free to comment in the thread. But I'll close it for now.

Closed 2021-03-18.

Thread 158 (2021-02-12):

Frame assembly instructions pdf - call out set screws in corner brackets

kelliead, 2021-02-12:
On the frame assembly instructions pdf, suggest including a note about preloading the M4x4mm set screws in the inside corner brackets prior to assembly.

It's not obvious to novice builders that the set screws come separately and need to be loaded into the brackets, and a few have gotten to the tightening step and realized there's nothing there to tighten. A simple note early in the instructions would save some confusion and time.

This would be helpful on sheet 3 of 28:

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

Poofjunior, 2021-03-15:
Ok, there is now a preloading page in the instructions that happens before this:
https://docs.google.com/viewer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

Closed 2021-03-15.

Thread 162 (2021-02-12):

Motor Plate Assembly instructions PDF: correct number of screws

kelliead, 2021-02-12:
Motor Plate Assembly instructions PDF:

Sheet 7 of 11 calls for six screws, but only four are used in the step:
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

The issue repeats again on sheet 11 of 11:
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

Poofjunior, 2021-03-15:
Good catch! Tis now fixed.

Closed 2021-03-15.

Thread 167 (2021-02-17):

Add a temperature Preheat to the Bed before probe in Beginning GCode

edskull, 2021-02-17:
Add M190 S[first_layer_bed_temperature] (or equivalent arguement if slicer allows) before the probe to reduce errors due to bed expansion

edskull, 2021-02-17:
Example:
G91 ; relative moves
G1 Z1 F900 ; raise tool 1mm
M140 S[first_layer_bed_temperature] ; Set Bed Temp
M104  S[first_layer_temperature_0] T[current_extruder] ; Set first tool temp
G90 ; absolute moves
T-1 ; Make sure nothing is parked on the carriage
G0 X150 Y150 F10000; Move to the center of the print area
M558 F500  ; Set the probing speed
M190 S[first_layer_bed_temperature] ; Wait for Bed Temp
G30 ; Do a single probe
M558 F50 ; Set a slower probing speed
G30 ; Do a second probe
G29 S1 ; Load Heightmap.csv
T[current_extruder]

Poofjunior, 2021-02-17:
Yeah; if this is supported in the slicer, we should definitely add a check like this. The bed probing is kind of a hack to fix this issue as-is, but waiting till the bed comes up to temperature before reprobing is a better approach.

edskull, 2021-02-21:
Thinking further on this, and im not sure if this is possible in firmware due to limitations, but one could use the Material information for the toolplate to calculate the difference between printing temperature and probing temperature. https://www.upmet.com/sites/default/files/datasheets/mic-6.pdf going from 20C to 80C for example would give a difference of around 0.036mm, negligible for most but i suppose for people doing high temp stuff this might become significant

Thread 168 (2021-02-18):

Fix Z-probe default Z-offset for RRF2 and RRF3

HaythamB, 2021-02-18:
In our default config files, we don't include a G31 command to account for the z-probe offsets, since we assume its the center of our tool coordinate offsets and its the center of our carriage.

However, due to legacy reasons, RRF defaults to a G31 Z0.7 **hardcoded in RRF** that must be addressed to get proper first layer behaviors, especially if using ZTATP for tool offset calculations in Z. (see forum post for details of why this occurs [here](https://forum.duet3d.com/topic/14609/why-0-7-z-offset-in-a-probe/4)

To test this out, unload your tools, rehome all your axes in RRF, and then issue a G30 S-1 command at the middle of your bed (or wherever your homez.g usually reads off of in your print space). You'll see that the trigger height consistently has an offset of 0.7mm applied to it!!

We should add a line to the config.g files to account for this oddity as follows: G31 Z0 (or alternatively more correctly: G31 K0 Z0), which will allow us to obtain a true reading of Z=0 when probing the bed.

This issue becomes even more apparent when aligning tools in Z using ZTATP, which will append this code to the endstop undefine/redefine steps it must take in order to use a touchplate. Without this code being in config.g, you must manually apply it every time you redefine your Z-probe code (M558 lines), which ZTATP does multiple times per tool.

olby, 2021-02-19:
The duet3 config contains a G31, we should make them consistent.

https://github.com/machineagency/jubilee/blob/e3cbce06f40137bf855db0f54141e2761347d4b3/software/duet_config_files/duet3/sys/config.g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

Poofjunior, 2021-02-25:
Oof; what a bug. Just tested this, and it looks like all of our tool offsets will need to be reduced by 0.7mm also. Not a big issue for people commissioning their machine for the first time, but it would be an adjustment for anyone blindly taking this setting. Thankfully, it defaults to making your tool 0.7mm too high, rather than too low.

Poofjunior, 2021-03-16:
Ok, this is fixed on Duet2 configs. I'll need another few days to test this out on a (work-in-progress) Duet3 machine

Poofjunior, 2021-03-23:
Ok; I got to thinking about this more recently. While it's a bummer that this is hardcoded into RRF, I think it's probably also saved countless Z limit switches on other machines running RRF.

Imagine if we set it to zero for a second. Then imagine we issue a **G0 X0 Y0 Z0** followed by literally any move in X or Y (but not Z). Since All mechanical switches need to be depressed slightly to trigger, that means that any move without carrying tools with Z=0 will be scraping the limit switch along the bed. While this probably wont happen to too many people, it's super easy to do but also super easy to check for in ZTATP.

I actually propose that in your ZTATP code, you (1) read the state of the Z offset with **G31** and (2) _then_ apply it in your offset calculations. This is super easy to read from the machine state by simply issuing the gcode command, and it has the bonus that it prevents us from prematurely killing more Z limit switches on the off-chance someone goes to Z=0 and then issues an X or Y move. Let me know what you think!

HaythamB, 2021-03-23:
I think this is a definitely win-win scenario. I'll add it to my ZTATP issues and handle it there. You're both correct that we should let the machine figure itself out without forcing the operator to think about Z crashes.

HaythamB, 2021-03-24:
Handled this in HaythamB/TAMV#11

Closed 2021-03-23.

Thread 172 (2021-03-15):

Thermal Fuses housing may be electrically conductive. AC Shock hazard.

HaythamB, 2021-03-15:
Some variants of TCO fuses come with a metal body, which is conductive for the full AC current loading of the silicone mat they're mated to. This can be an electrical hazard to users, and should be highlighted in the installation notes/warnings to avoid anyone getting a nasty jolt if they're tempted to touch the fuse while in operation.

Its essentially an exposed AC mains terminal, and needs to be treated accordingly.

Poofjunior, 2021-03-16:
ok, for the one spec'ed as optional in the wiring diagram, it's some sort of electrically insulating material (7MegaOhms according to my multimeter.) I think we're in the clear since it's not only high resistance; it's also meant to be clamped such that it's touching the silicone pad, not the metal plate.

Closed 2021-03-16.

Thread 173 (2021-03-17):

Parking post note is wrong

Poofjunior, 2021-03-17:
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

Second note is pointing to the wrong screws!

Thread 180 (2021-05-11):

X Axis Hard Stop

Poofjunior, 2021-05-11:
A Limit Switch Saver

Adding a post (cylindrical spacer) through the *last* MGN12H hole would introduce a hard-stop on the lower end of the x-axis. if sized correctly, we could probabaly save misconfigured limit switches from getting depressed past their trigger range.
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

Poofjunior, 2021-05-18:
Ok; I think I'm onto something. It turns out that adding another piece at the bottom is much easier than modifying the carriage.

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

Poofjunior, 2021-06-03:
Ok, this is now in the main branch with the corexy instructions updated.
https://github.com/machineagency/jubilee/blob/main/frame/fabrication_exports/3d_printed_parts/frame/x_axis_hard_stop.STL

Closed 2021-06-03.

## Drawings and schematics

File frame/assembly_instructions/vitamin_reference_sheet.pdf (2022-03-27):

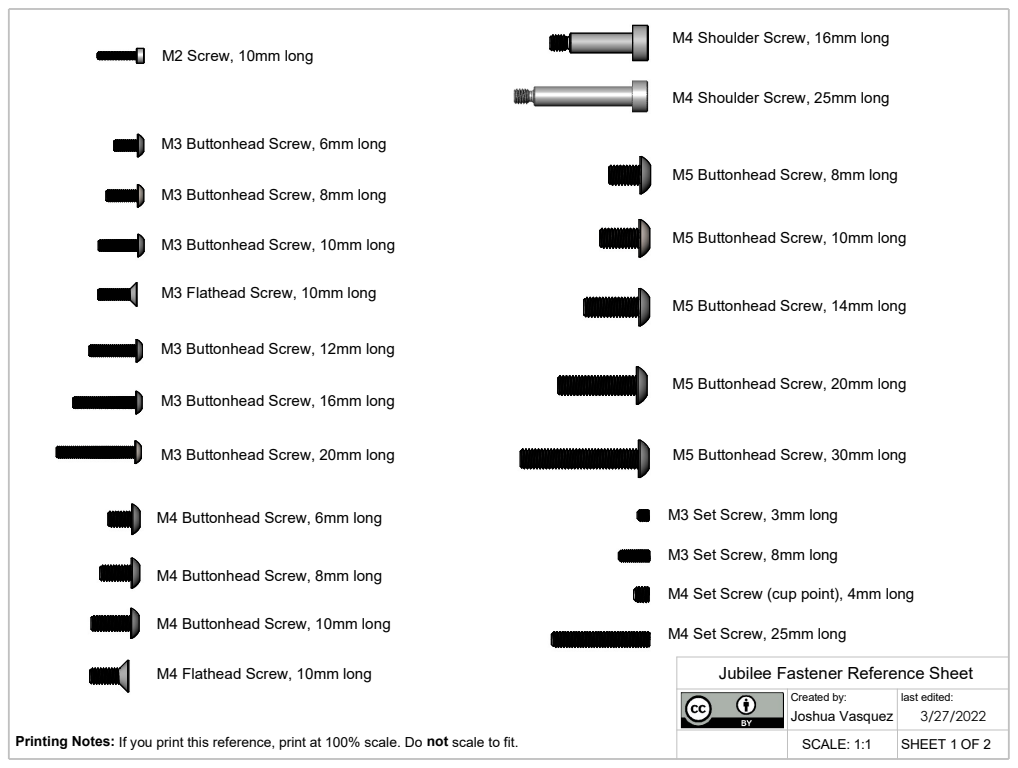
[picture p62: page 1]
M3 Buttonhead Screw, 20mm long; M5 Buttonhead Screw, 30mm long; M2 Screw, 10mm long

M4 Shoulder Screw, 16mm long

M4 Shoulder Screw, 25mm long

M3 Buttonhead Screw, 6mm long

M5 Buttonhead Screw, 8mm long

M3 Buttonhead Screw, 8mm long

M5 Buttonhead Screw, 10mm long

M3 Buttonhead Screw, 10mm long

M3 Flathead Screw, 10mm long

M5 Buttonhead Screw, 14mm long

M3 Buttonhead Screw, 12mm long

M5 Buttonhead Screw, 20mm long

M3 Buttonhead Screw, 16mm long

M4 Buttonhead Screw, 6mm long

M3 Set Screw, 3mm long

M3 Set Screw, 8mm long

M4 Buttonhead Screw, 8mm long

M4 Set Screw (cup point), 4mm long

M4 Buttonhead Screw, 10mm long

M4 Set Screw, 25mm long

Jubilee Fastener Reference Sheet

M4 Flathead Screw, 10mm long

Created by: Joshua Vasquez | last edited: 3/27/2022

Printing Notes: If you print this reference, print at 100% scale. Do not

scale to fit.

SCALE: 1:1 | SHEET 1 OF 2

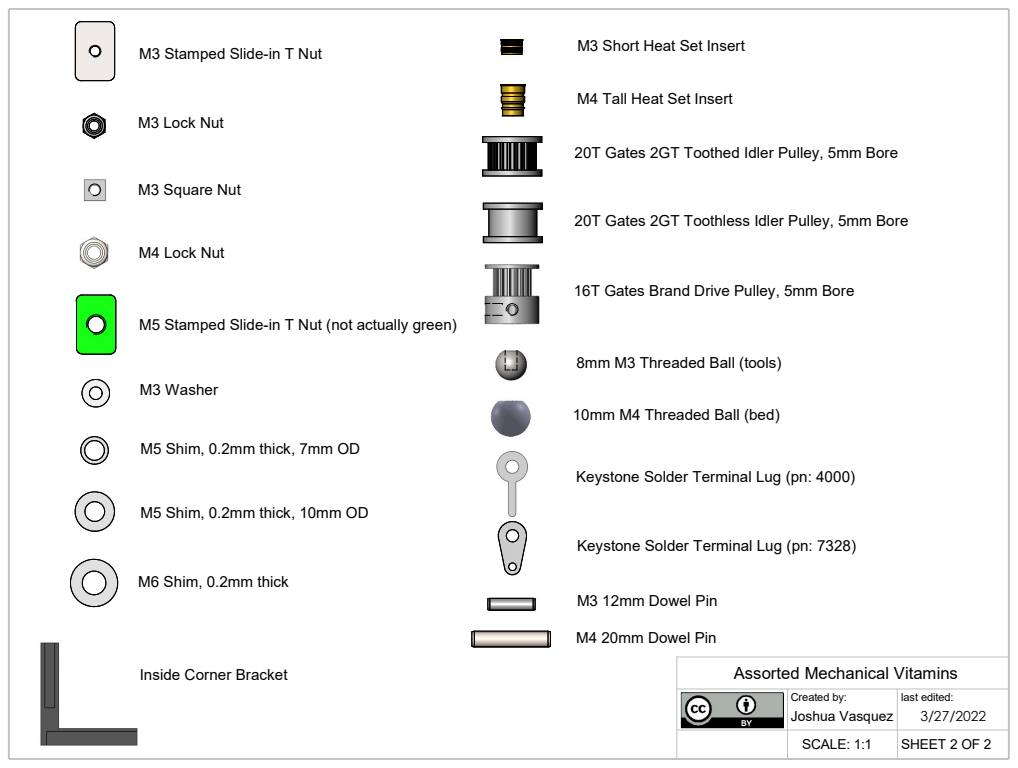
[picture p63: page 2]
M6 Shim, 0.2mm thick; M4 20mm Dowel Pin; M3 12mm Dowel Pin; M3 Square Nut; M3 Lock Nut; M4 Lock Nut; M3 Washer

M3 Short Heat Set Insert

M3 Stamped Slide-in T Nut

M4 Tall Heat Set Insert

20T Gates 2GT Toothed Idler Pulley, 5mm Bore

20T Gates 2GT Toothless Idler Pulley, 5mm Bore

16T Gates Brand Drive Pulley, 5mm Bore

M5 Stamped Slide-in T Nut (not actually green)

8mm M3 Threaded Ball (tools)

10mm M4 Threaded Ball (bed)

M5 Shim, 0.2mm thick, 7mm OD

Keystone Solder Terminal Lug (pn: 4000)

M5 Shim, 0.2mm thick, 10mm OD

Keystone Solder Terminal Lug (pn: 7328)

Assorted Mechanical Vitamins

Inside Corner Bracket

Created by: Joshua Vasquez | last edited: 3/27/2022

SCALE: 1:1 | SHEET 2 OF 2

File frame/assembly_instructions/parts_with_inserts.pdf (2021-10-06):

B B

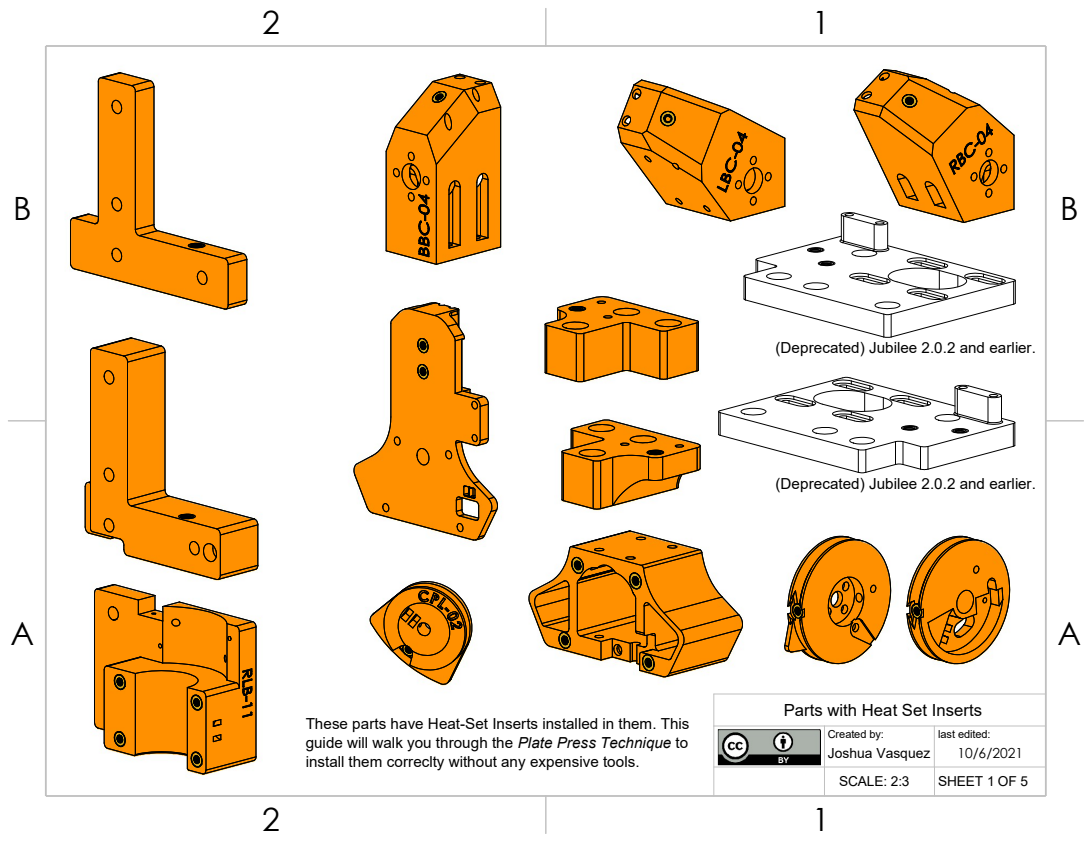
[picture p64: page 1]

(Deprecated) Jubilee 2.0.2 and earlier.

Parts with Heat Set Inserts

These parts have Heat-Set Inserts installed in them. This
guide will walk you through the Plate Press Technique to
install them correclty without any expensive tools.

Created by: Joshua Vasquez | last edited: 10/6/2021

SCALE: 2:3 | SHEET 1 OF 5

B B

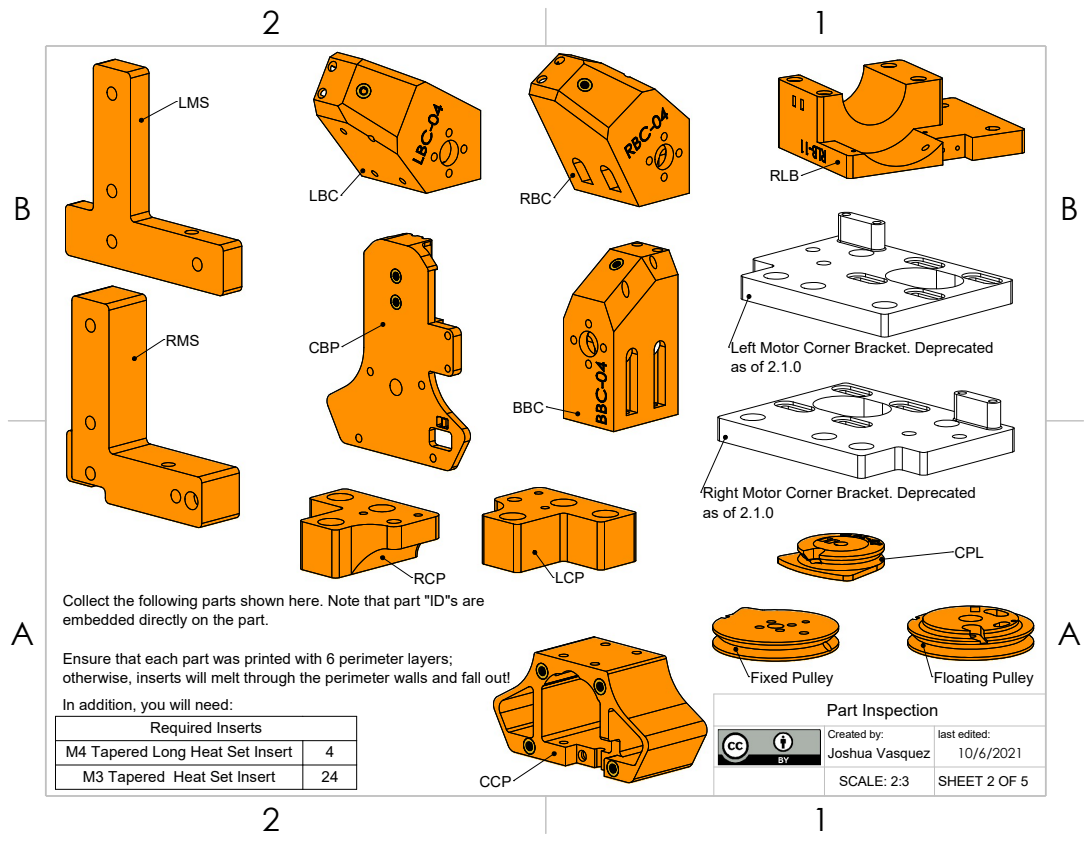
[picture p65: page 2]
SCALE: 2:3; SHEET 2 OF 5; Part Inspection; RLB; Required Inserts; M3 Tapered Heat Set Insert; RMS; LMS; Floating Pulley; RBC; CBP; BBC; RCP; LCP; LBC; Fixed Pulley; CPL; CCP

Left Motor Corner Bracket. Deprecated

Right Motor Corner Bracket. Deprecated

Collect the following parts shown here. Note that part "ID"s are
embedded directly on the part.

Ensure that each part was printed with 6 perimeter layers;
otherwise, inserts will melt through the perimeter walls and fall out!
In addition, you will need:

Created by: Joshua Vasquez | last edited: 10/6/2021

M4 Tapered Long Heat Set Insert | 4

Created by: Joshua Vasquez | last edited: 10/6/2021
SCALE: 3:4 | SHEET 3 OF 5

The Plate Press Technique Overview

A A

B B

1) Heat up the Soldering Iron. (a special tip is recommended, but not required.)
2) With the insert pre-placed over the hole, gently touch the iron to the insert. Let the weight of the iron gently push the insert into the hole. This process should take about 10-15 seconds.
3) When the insert is about 90% inserted, remove the iron. Quickly either:
(a) flip the part upside down onto a heat resistant surface, or
(b) push any flat metal surface (such as a razor blade) onto the insert and push it completely down. Wait 5 seconds for the insert to cool in this position.
4) That's it! Your insert is installed at the proper height and angle.

B B

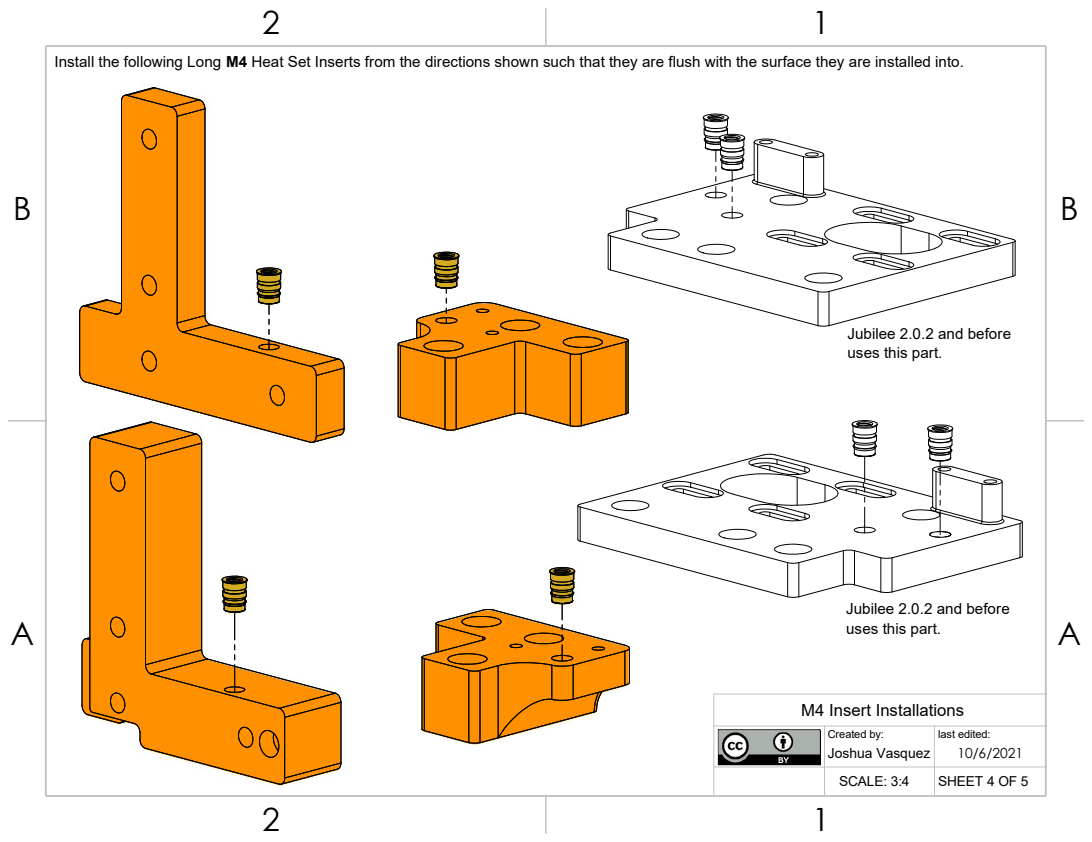
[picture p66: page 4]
M4 Insert Installations

Install the following Long M4 Heat Set Inserts from the directions shown such that they are flush with the surface they are installed into.

Jubilee 2.0.2 and before
uses this part.

Created by: Joshua Vasquez | last edited: 10/6/2021

SCALE: 3:4 | SHEET 4 OF 5

B B

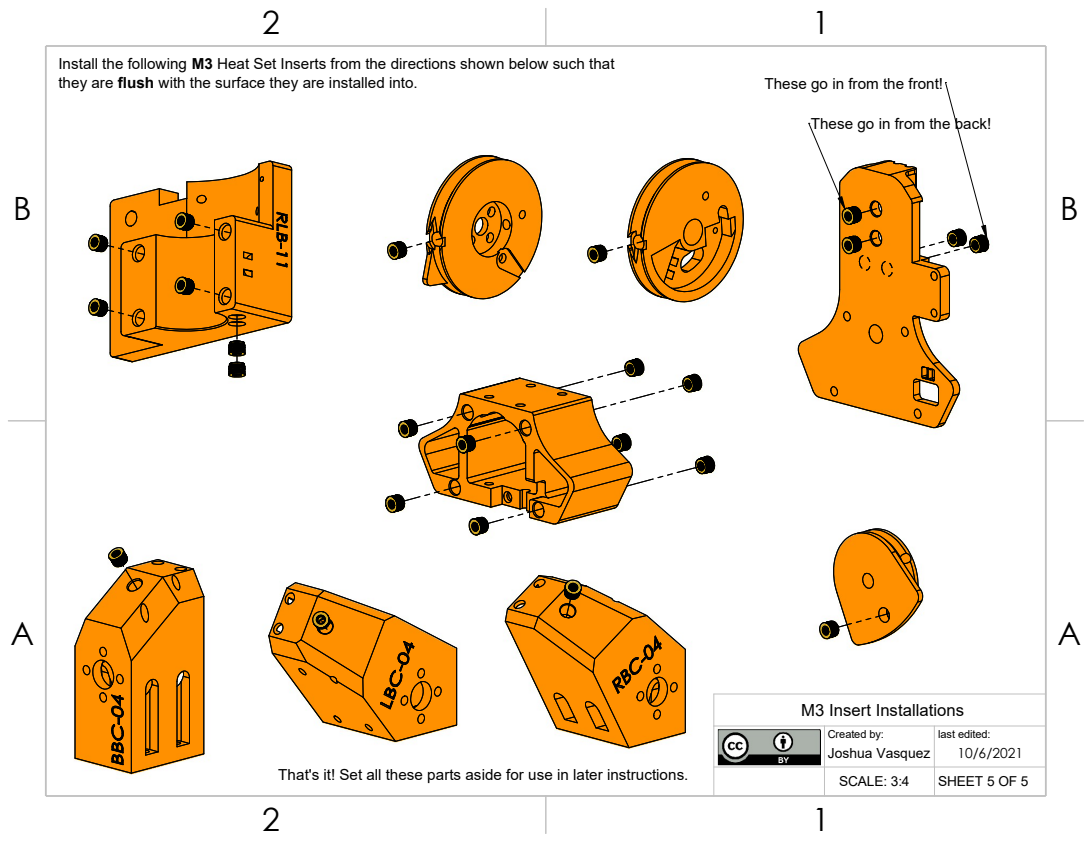
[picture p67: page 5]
M3 Insert Installations

Install the following M3 Heat Set Inserts from the directions shown below such that
they are flush with the surface they are installed into.

These go in from the front!

These go in from the back!

Created by: Joshua Vasquez | last edited: 10/6/2021

That's it! Set all these parts aside for use in later instructions.

SCALE: 3:4 | SHEET 5 OF 5

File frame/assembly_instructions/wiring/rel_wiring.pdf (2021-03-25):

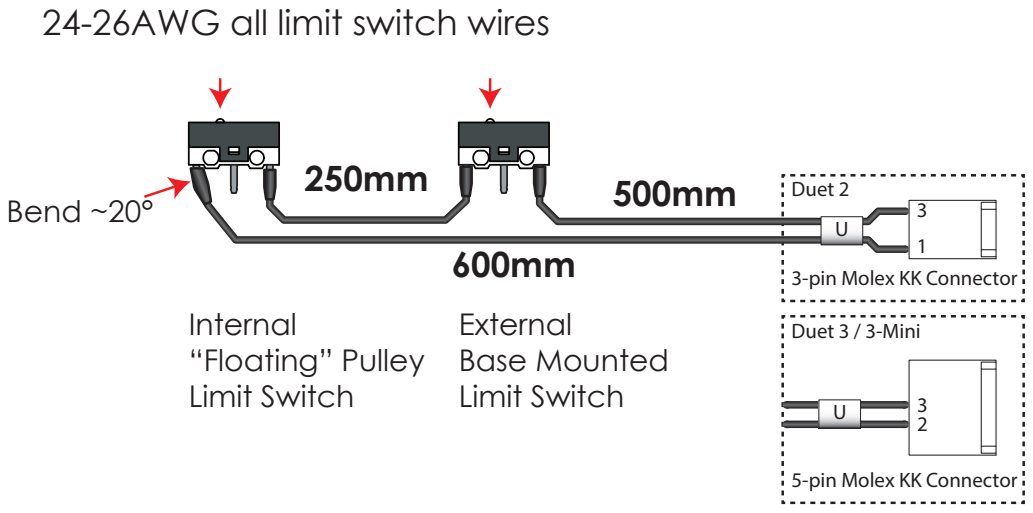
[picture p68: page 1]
External Base Mounted Limit Switch; Internal “Floating” Pulley Limit Switch; Bend ~20°; Duet 2; Duet 3 / 3-Mini

24-26AWG all limit switch wires

3-pin Molex KK Connector

5-pin Molex KK Connector

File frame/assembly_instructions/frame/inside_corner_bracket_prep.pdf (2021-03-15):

B B

2

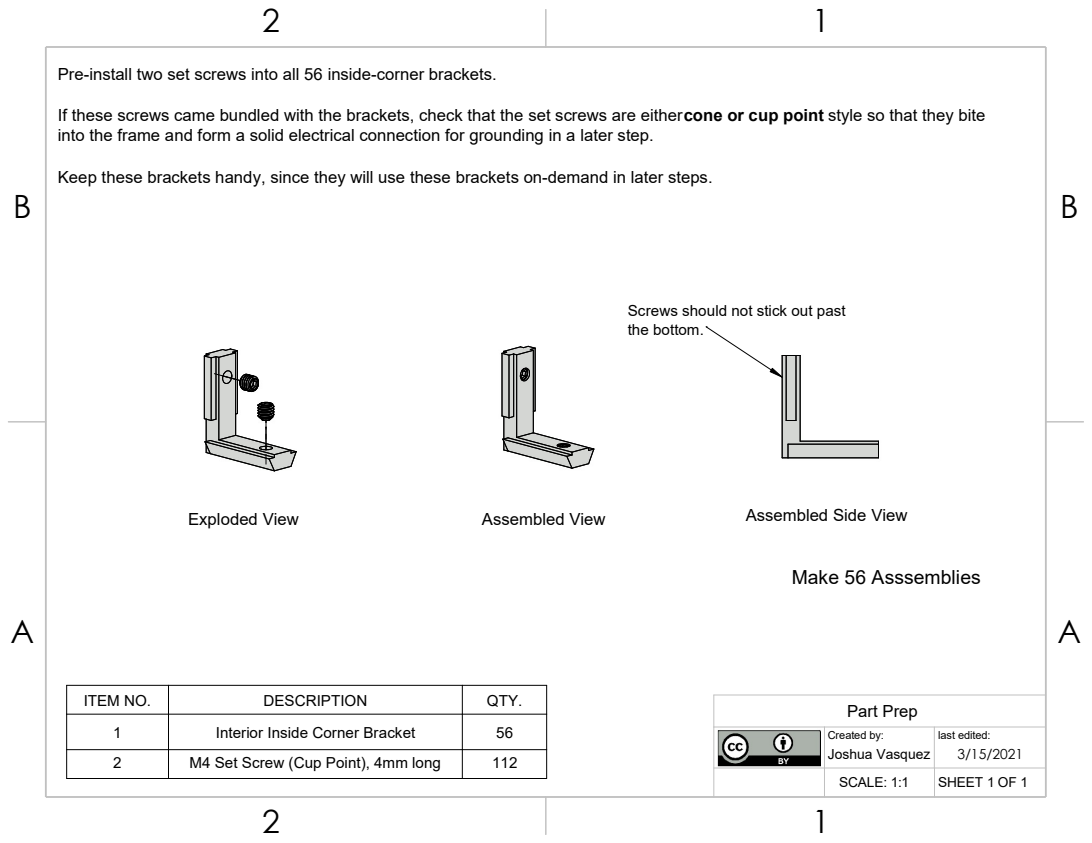
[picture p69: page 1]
Part Prep ITEM NO.; DESCRIPTION; QTY.; Exploded View; Assembled View; Assembled Side View; Make 56 Asssemblies

Pre-install two set screws into all 56 inside-corner brackets.

If these screws came bundled with the brackets, check that the set screws are either cone or cup point style so that they bite
into the frame and form a solid electrical connection for grounding in a later step.

Keep these brackets handy, since they will use these brackets on-demand in later steps.

Screws should not stick out past
the bottom.

1 | Interior Inside Corner Bracket | 56
2 | M4 Set Screw (Cup Point), 4mm long | 112

Created by: Joshua Vasquez | last edited: 3/15/2021

SCALE: 1:1 | SHEET 1 OF 1

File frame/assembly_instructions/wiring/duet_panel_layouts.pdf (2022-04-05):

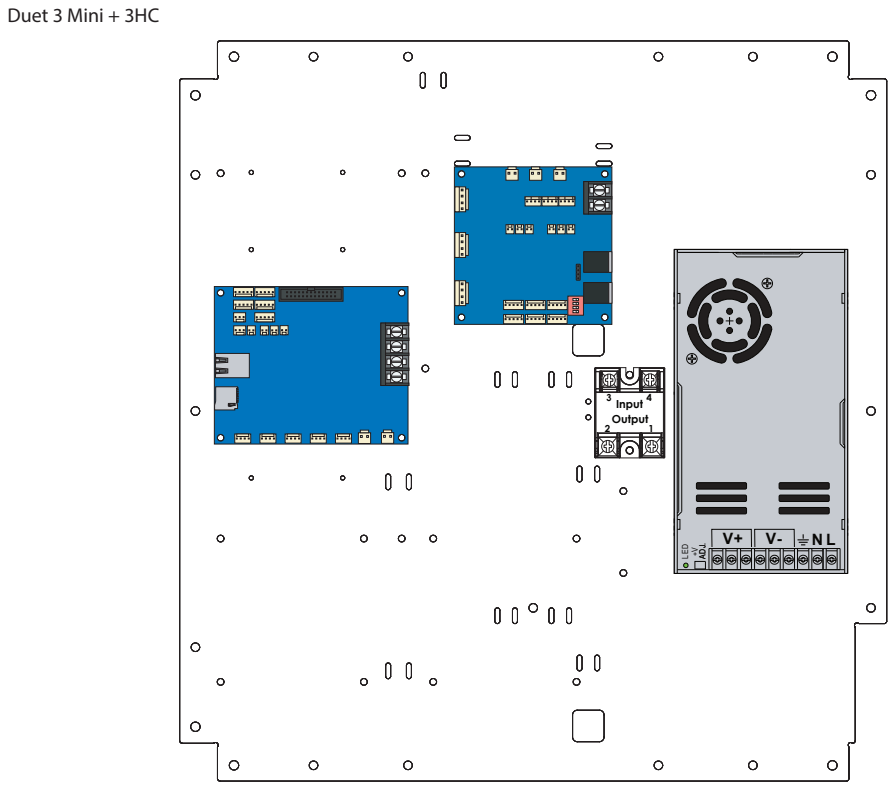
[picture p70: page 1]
ADJ.; Input Output; Duet 3 Mini + 3HC

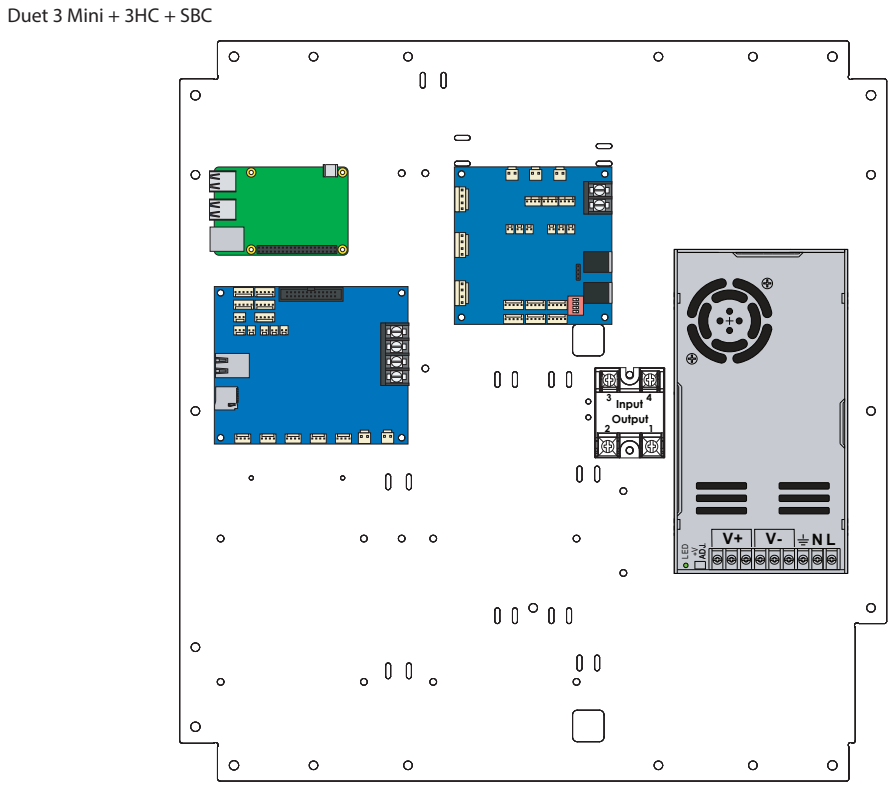
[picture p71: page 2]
ADJ.; Input Output

Duet 3 Mini + 3HC + SBC

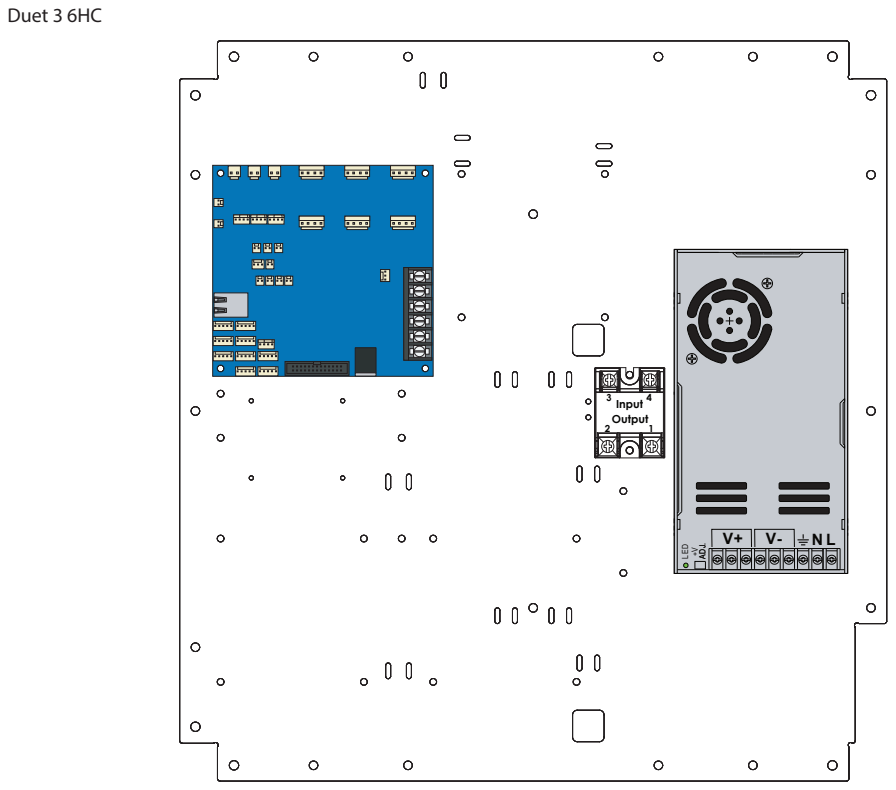
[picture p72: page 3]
ADJ.; Input Output; Duet 3 6HC

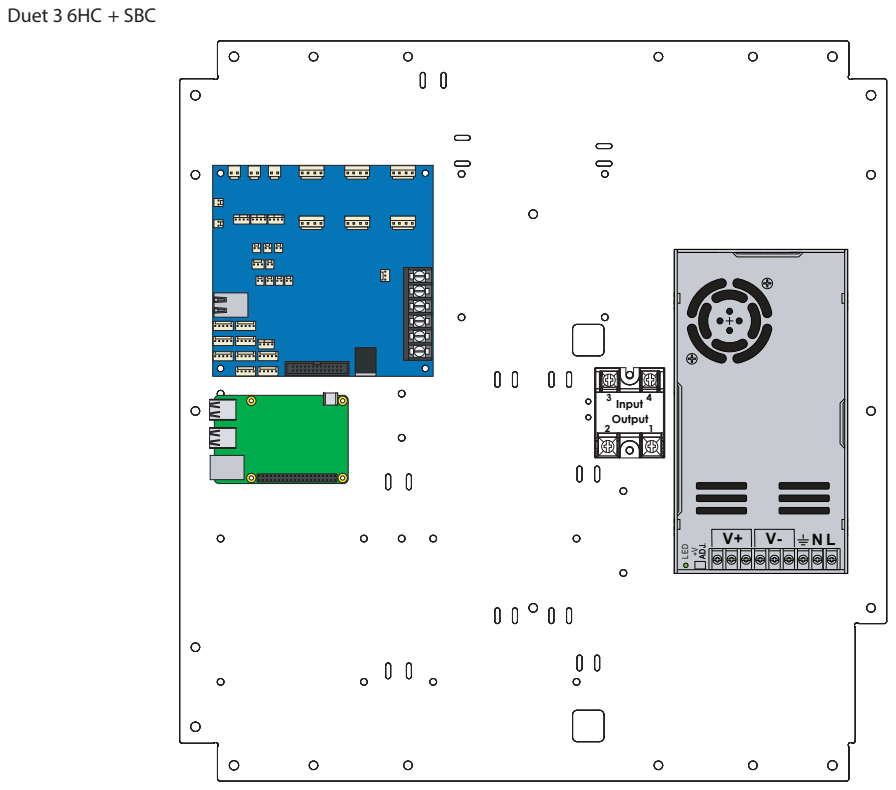
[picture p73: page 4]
ADJ.; Input Output; Duet 3 6HC + SBC

ADJ.; Input Output; Duet 2 + Duex5

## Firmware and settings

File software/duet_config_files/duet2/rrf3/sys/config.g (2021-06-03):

; Jubilee 2.2.0 Config File for RepRapFirmware 3

; Name and Identification
M550 P"Jubilee"                         ; Machine name and Netbios name

; Networking. For more info on this connection setup, see:
; https://jubilee3d.com/index.php?title=Connecting_to_Jubilee
M552 P192.168.1.2 S1                    ; Use Ethernet with a static IP
M554 192.168.1.3                        ; Gateway
M553 P255.255.255.0                     ; Netmask
M586 P1 S1                              ; Enable FTP
M586 P2 S1                              ; Enable Telnet

; Debugging
M111 S0                                 ; Debug off
M929 P"eventlog.txt" S1                 ; Start logging to file eventlog.txt

; General Preferences
M555 P2                                 ; Set Marlin-style output
G21                                     ; Set dimensions to millimetres
G90                                     ; Send absolute coordinates...
M83                                     ; ...but relative extruder moves

; Motor Drives
M584 X0 Y1 Z6:7:8 E3:4 U2   ; Map Z to drivers 6, 7, 8. Map extruders to 3 and 4. Create Toolchanger Lock axis.

M569 P0 S0                  ; Drive 0 direction | X stepper
M569 P1 S0                  ; Drive 1 direction | Y Stepper

M569 P6 S0                  ; Drive 6 direction | Front Left Z
M569 P7 S0                  ; Drive 7 direction | Front Right Z
M569 P8 S0                  ; Drive 8 direction | Back Z

M569 P2 S0                  ; Drive 2 direction | Toolchanger Actuator

M569 P3 S0 D2               ; Drive 3 direction | Extruder 0 in Spreadcycle Mode
M569 P4 S0 D2               ; Drive 4 direction | Extruder 1 in Spreadcycle Mode

; Joint Kinematics
M669 K1                                 ; CoreXY mode

; Kinematic bed ball locations.
; Locations are extracted from CAD model assuming lower left build plate corner is (0, 0) on a 305x305mm plate.
M671 X297.5:2.5:150 Y313.5:313.5:-16.5 S10 ; Front Left: (297.5, 313.5) | Front Right: (2.5, 313.5) | Back: (150, -16.5)


; XYZUE Axis Configuration
M350 X16 Y16 Z16 E16 U4 I1              ; Set 16x microstepping for xyz axes & extruder, 4x for toolchanger lock. Use interpolation.

M906 X2405 Y2405                        ; Motor currents XY (mA). 2405mA is 85% of 2828mA Peak current. (2828mA peak is 2000mA RMS)
M906 Z1600                              ; LDO ZZZ Motor Currents (mA).
M906 U670 I60                           ; (Default) LDO-28STH32-0674APG14 Toolchanger Lock motor current (mA) and idle motor percentage.
;M906 U540 I60                           ; (Alternate) LDO-28STH51-0674APG14 Toolchanger Lock motor current (mA) and idle motor percentage.
;M906 U900 I60                           ; (Old) 14HS13-0804S-PG5 StepperOnline Toolchanger Lock motor current (mA) and idle motor percentage
                                        ; Note: Idle current setting is common across all motors (XYZZZU).

M201 X1200 Y1200                        ; XY Accelerations (mm/s^2). (Can be bumped up to 2000+)
M201 Z100                               ; ZZZ Acceleration
M201 U800                               ; U Accelerations (mm/s^2)

M203 X18000 Y18000 E8000 U9000          ; Maximum X, Y, E, U axis speeds (mm/min)
M203 Z800                               ; Maximum Z axis speed with T8x2 leadscrew and 0.9mm stepper
;M203 Z1600                              ; Maximum Z axis speed with T8x4 leadscrew and 0.9mm stepper
M566 X1000 Y1000 Z500 E3000 U50         ; Maximum jerk speeds (mm/min)

M92 X200 Y200                           ; Steps/mm for X,Y for 16x microstepping & 16T pulley
;M92 Z3200                               ; Steps/mm for Z with a T8x2 leadscrew and 0.9mm stepper. (16 * 400)/2
M92 Z1600                               ; Steps/mm for Z with a T8x4 leadscrew and 0.9mm stepper. (16 * 400)/4
M92 U30.578                             ; Steps/deg for U from (200 * 4 * 13.76)/360

; Set axis software limits and min/max switch-triggering positions.
; Adjusted such that (0,0) lies at the lower left corner of a 300x300mm square in the 305mmx305mm build plate.
M208 X-13.75:313.75 Y-44:341 Z-0.2:305
M208 U0:200                                 ; Set Elastic Lock (U axis) max rotation angle

; Machine Thermistors
M308 S0 P"bed_temp" Y"thermistor" T100000 B3950 R4700 ; Define built-in Keenovo Bed Thermistor values.
;M308 S0 P"bed_temp" Y"thermistor" T10000 B3435 ; Define BOM-specified replaceable bed thermistor (with adjusted B value)
M308 S4 Y"drivers" A"DRIVERS"           ; Define sensor 4 as temperature warning and overheat flags on the TMC2660 on Duet
M308 S5 Y"mcu-temp" A"MCU"              ; Define sensor 5 as thermistor on pin e1temp for left stepper

; Machine Heaters
M570 S30                                    ; Print will be terminated if a heater fault is not reset within 30 minutes.
M950 H0 C"bed_heat" T0 						 ; heater 0 uses the bed_heat pin, sensor 0
M140 H0										 ; the bed heater is heater 0
M143 H0 S100                                 ; Maximum H0 (Bed) heater temperature

;Settings for running a mesh bed leveling procedure:
M557 X10:290 Y10:290 P6

; Machine Switches
M574 X1 S1 P"^xstop"   ; X min active high endstop switch
M574 Y1 S1 P"^ystop"   ; Y min active high endstop switch
M574 Z1 S1 P"^zstop"   ; Z min active high endstop switch
M574 U1 S1 P"^e0stop"  ; U "min/max" active high endstop switch

; Z probing settings
M574 Z0 P"nil" ; no Z endstop switch, free up Z endstop input
M558 P5 C"^zstop" H5 A1 T10000 S0.02; Z probe connected to Z endstop input
; P5 --> probe type: switch
; C2 --> endstop number
; H5 --> dive height
; A1 --> max number of times to probe
; T100000 --> travel speed between probe points
; S0.02 --> tolerance when probing multiple times
G31 K0 X0 Y0 Z-2        ; Set the limit switch position as the  "Control Point."
                        ; Note: the switch free (unclicked) position is 7.2mm,
                        ; but the operating position (clicked) is 6.4 +/- 0.2mm. 
                        ; A 1mm offset (i.e: 7.2-6.2 = 1mm) would be the 
                        ; Z to worst-case free position, but we add an extra 1mm
                        ; such that XY travel moves across the bed when z=0
                        ; do *not* scrape or shear the limit switch.


; Definitions for Components of 2x Extruders
M906 E1250:1250                         ; Motor currents (mA) for both extruders drives
M201 E1300:1250                         ; E Acceleration (mm/s^2)
M203 E8000:8000                         ; Maximum axis speeds (mm/min)
M566 E3000:3000                         ; Maximum jerk speeds (mm/min)
M92 E830:830                            ; BMG Extruder - 0.9 deg/step Tool0:Tool1
M308 S1 P"spi.cs1" Y"rtd-max31865"      ; define PT100-style E0 temperature sensor
M308 S2 P"spi.cs2" Y"rtd-max31865"      ; define PT100-style E1 temperature sensor
;M308 S1 P"e0_temp" Y"pt1000"           ; define PT1000-style E0 temperature sensor
;M308 S2 P"e1_temp" Y"pt1000"           ; define PT1000-style E1 temperature sensor
M143 H1 S260                            ; Maximum H1 (Extruder 0) heater temperature
M143 H2 S260                            ; Maximum H2 (Extruder 1) heater temperature
M950 F0	C"fan0"                         ; Fan 0, part cooler fan on Tool 0
M950 F1 C"fan1"                         ; Fan 1, part cooler fan on Tool 1
M950 H1 C"e0_heat" T1                   ; heater 1 uses the e0_heat pin and sensor 1
M950 H2 C"e1_heat" T2                   ; heater 2 uses the e1_heat pin and sensor 2

M563 P0 S"Extruder 0" D0 H1 F0          ; Define tool 0. Group drive, heater, and part fan.
G10 P0 X-4.5 Y44.02 Z-5.16              ; Set tool 1 XYZ offset from the Control Point (Z Probe).
                                        ; XYZ Offsets are unique to your machine.
G10 P0 S210 R190                        ; Set tool 0 operating and standby temperatures(-273 = "off")
M572 D0 S0.05                           ; Set pressure advance on Extruder Drive 0
; Note: Hotend fan is plugged into always-on port

M563 P1 S"Extruder 1" D1 H2 F1          ; Define tool 1. Group drive, heater, and part fan.
G10 P1 X-5.36 Y44.7 Z-2.22              ; Set tool 1 XYZ offset from the Control Point (Z Probe)
                                        ; XYZ Offsets are unique to your machine.
G10 P1 S210 R210                        ; Set tool 1 operating and standby temperatures(-273 = "off")
M572 D1 S0.025                          ; Set pressure advance on Extruder Drive 1
; Note: Hotend fan is plugged into always-on port


M593 P1 F27  ; ZVD input shaper at 27Hz (RRF 3.3+)

M501                                    ; Load saved parameters from non-volatile memory

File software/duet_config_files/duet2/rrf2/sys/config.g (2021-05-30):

; Jubilee 2.1.1 Config File
; drawing inspiration from the Railcore 300ZL config file

; Name and Identification
M550 P"Cubilee"                         ; Machine name and Netbios name

; Networking
M552 P192.168.1.2 S1                    ; Use Ethernet with a static IP
M554 192.168.1.3                        ; Gateway
M553 P255.255.255.0                     ; Netmask
M586 P2 S1                              ; Enable Telnet

; Debugging
M111 S0                                 ; Debug off
M929 P"eventlog.txt" S1                 ; Start logging to file eventlog.txt

; General Preferences
M555 P2                                 ; Set Marlin-style output
G21                                     ; Set dimensions to millimetres
G90                                     ; Send absolute coordinates...
M83                                     ; ...but relative extruder moves

; Joints
M584 X0 Y1 Z6:7:8 E3:4:5:9 U2   ; Map Z to drives 6, 7, 8. Map extruders to 3 and 4. Create Toolchanger Lock axis.

M569 P0 S0                  ; Drive 0 direction | X stepper
M569 P1 S0                  ; Drive 1 direction | Y Stepper

M569 P6 S0                  ; Drive 6 direction | Front Left Z
M569 P7 S0                  ; Drive 7 direction | Front Right Z
M569 P8 S0                  ; Drive 8 direction | Back Z

M569 P2 S0                  ; Drive 2 direction | Toolchanger Actuator

M569 P3 S0 D2               ; Drive 3 direction | Extruder 0 in SpreadCycle Mode
M569 P4 S0 D2               ; Drive 4 direction | Extruder 1 in SpreadCycle Mode


; Joint Kinematics
M669 K1                                 ; CoreXY mode

; Kinematic bed ball locations. Locations are extracted from CAD model assuming:
;   300x300mm build region offset evenly from the 305x305mm plate.
;   back right corner of build region is (0, 0).
M671 X297:2.5:150 Y313.5:313.5:-16.5 S10 ; Front Left: (297.5, 313.5) | Front Right: (2.5, 313.5) | Back: (150, -16.5)


; Axis and Motor Configuration
M350 X16 Y16 Z16 E16 U4 I1              ; Set 16x microstepping for xyz axes & extruder, 4x for toolchanger lock. Use interpolation.
M574 X1 Y1 Z1 S1                        ; Set homing switch configuration x low-end, y low-end, z low-end, all active-high (NC)
M574 U1 S1                              ; Set homing switch configuration for toolchange lock. Both switches should be wired NC and in series.

M906 X2263 Y2263                        ; LDO XY motor currents (mA). 2263mA is 80% of 2828mA Peak Current. (2828mA Peak is 2000mA RMS)
                                        ; Do not exceed 90% of full XY motor current rating without heatsinking the XY motor drivers.
;M906 X1900 Y1900                       ; StepperOnline XY motor currents (mA)
M906 Z1600                              ; LDO ZZZ Motor currents (mA). Conservative.
;M906 Z1750                             ; StepperOnline ZZZ motor currents (mA)

M906 E1250                              ; Motor currents E (mA)

M906 U670 I60                           ; LDO Toolchanger Elastic Lock motor current (mA) and idle motor percentage.
;M906 U900 I60                          ; StepperOnline Toolchanger Elastic Lock motor current (mA) and idle motor percentage
                                        ; Note: Idle current setting is common across all motors (XYZZZU).

M201 X1000 Y1000                        ; XY Acceleration. Conservative. 1500+ possible.
M201 Z100                               ; LDO ZZZ Acceleration
;M201 Z100                               ; StepperOnline Z Acceleration
M201 E1300                              ; E Acceleration
M201 U800                               ; LDO U Accelerations (mm/s^2) conservative

M203 X13000 Y13000 Z800 E8000 U9000     ; Maximum speeds (mm/min) conservative. 18000+ possible on XY. Depends on tool.
M566 X1000 Y1000 Z500 E3000 U50          ; Maximum jerk speeds mm/minute

M92 X200 Y200                           ; Steps/mm for X,Y

M92 U30.578                             ; Steps/deg for U from (200 * 4 * 13.76)/360
M92 Z3200                               ; Steps/mm for Z for a T8x2 leadscrew and 0.9mm stepper. (16 * 400)/2
;M92 Z1600                               ; Steps/mm for Z for a T8x4 leadscrew and 0.9mm stepper. (16 * 400)/4
M92 E830                                ; Extruder - 0.9 deg/step

; Set axis software limits and min/max switch-triggering positions.
; Adjusted such that (0,0) lies at the upper right corner of a 300x300mm square in the 305mmx305mm build plate.
M208 X-13.75:313.75 Y-44:341 Z-0.2:305
M208 U0:200                                 ; Set Elastic Lock (U axis) max rotation angle

;Mesh Bed Leveling Settings:
M557 X10:290 Y10:290 P6

; Z probing settings
M558 P4 C2 H5 A1 T10000  S0.02
; P4 --> probe type: switch
; C2 --> endstop number
; H5 --> dive height
; A1 --> max number of times to probe
; T100000 --> travel speed between probe points
; S0.02 --> tolerance when probing multiple times
G31 K0 X0 Y0 Z-2    ; Set the limit switch position as the  "Control Point."
                    ; Note: the switch free (unclicked) position is 7.2mm,
                    ; but the operating position (clicked) is 6.4 +/- 0.2mm. 
                    ; A 1mm offset (i.e: 7.2-6.2 = 1mm) would be the 
                    ; Z to worst-case free position, but we add an extra 1mm
                    ; such that XY travel moves across the bed when z=0
                    ; do *not* scrape or shear the limit switch.

; Thermistors
M305 P0 S"Bed" T10000 B3435 H0                ; BOM-specified Adjusted Terminal Lug Thermistor values.
;M305 P0 S"Bed" T10000 B3984 H0 L160          ; BOM-specified Terminal Lug Thermistor values.
;M305 P0 S"Bed" T100000 B3950 R4700 H0 L0    ; Built-in Keenovo Bed Thermistor values.

; PT100 Hotend Temperature Sensors. These require an external Breakout Board. For other configs, see the wiki:
; https://jubilee3d.com/index.php?title=Bondtech_Direct_Drive_Extruder 
M305 P1 X200                                ; Map Extruder 0 sensor to PT100 Channel 0
M305 P2 X201                                ; Map Extruder 1 sensor to PT100 Channel 1

;Heaters
M570 S30                                    ; Print will be terminated if a heater fault is not reset within 30 minutes.
M143 H0 S100                                ; Maximum H0 (Bed) heater temperature
;M143 H1 S260                                ; Maximum H1 (Extruder) heater temperature

; Default heater model
M307 H0 A270.7 C90.4 D6.7 B0 S1.0           ; Default Bed Heater Parameters, before tuning / if config-override.g is missing

; Tool definitions
M563 P0 S"Extruder 0" D0 H1 F0          ; Define tool 0
G10 P0 X-4.5 Y44.02 Z-5.62              ; Set tool 0 offset from the bed
G10 P0 S190 R170                        ; Set tool 0 operating and standby temperatures(-273 = "off")
M572 D0 S0.1				; Set pressure advance on Extruder Drive 0

M563 P1 S"Extruder 1" D1 H2 F2          ; Define tool 1
G10 P1 X-4.23 Y45.60 Z-2.51             ; Set tool 1 offset from the bed with tool-0 as a reference.
G10 P1 S190 R170                        ; Set tool 1 operating and standby temperatures(-273 = "off")
M572 D1 S0.1                            ; Set pressure advance on Extruder Drive 1

; Fans
M106 P0 S0                               ; Turn off fan 0
;M106 P1 S0                               ; Turn off fan 1


M593 F33.33  ; Reduce resonances at 33Hz based on XY vibration pattern on prints. This value could use a second opinion.

M98 P"config-user.g"                    ; Load custom user config

M501                                    ; Load saved parameters from non-volatile memory

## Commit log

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2019-12-26 fixed frame instruction typos and added updated fixture STL
    [z_lift_pin_insertion_fixture.STL]
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2020-01-09 adding first pass at new configs for jubilee2
    [bed.g, config.g, tfree0.g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]
2020-01-14 adding build plate instructions; adding extra zip tie holes to back panel.
    [back_z_motor_plate.STL, duet_2_and_3_electronics_back_panel.DXF]
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2020-01-21 updating cad with fixed carriage back plate.
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2020-01-23 updating instructions with Keep Nut fix
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2020-01-27 moving printed part stls for tools to respective tool folder
    [blower_fan_shroud.STL, bondtech_bmg_adaptor_plate.STL, groovemount_clip.STL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]
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2020-01-30 adding missing screw sizes
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2020-02-01 removing extruder fan interference
    [blower_fan_shroud.STL, tool_plate.STL]
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2020-02-20 changing STL file format type for faster download
    [z_lift_pin_insertion_fixture.STL]
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2020-02-25 swapping motor clip stl to ascii
    [lock_actuator_motor_clip.STL]
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2020-03-13 updating all printed parts for Gates belt compatibilitiy
    [back_bed_coupling_lift.STL, back_left_pulley_reinforcement_plate.STL, back_right_pulley_reinforcement_plate.STL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]
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2020-03-30 correcting 3296
    [tpost0.g]
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2020-04-12 updating steps/mm for stepper-online U motor in config
    [config.g]
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2020-04-12 updating carriage instructions, STL orientation, and changelog with proper STL links
    [motor_reinforcement_plate.STL]
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2020-04-13 Beta version of Duet3 files
    Orignal Authors Joshua Vasquez for Duet 2 and Danal to Duet 3
    [Toffsets.g, bed.g, cancel.g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]
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2020-04-22 updating machined motor plates and z axis instructions
    [left_alum_double_pulley_corner_bracket.STEP, left_alum_motor_corner_bracket.STEP, machined_corner_pulley_plate.STEP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]
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2020-04-28 hotfixing corner pulley plates and adding wiring diagram
    [back_pulley_reinforcement_plate.SLDPRT, crossbar_pulley_reinforcement_plate.SLDPRT, left_corner_pulley_reinforcement_plate.STL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]
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2020-04-28 crossbar screw length fix
2020-05-04 Revert "Merge remote-tracking branch 'upstream/master'"
    This reverts commit 2311f67b2bdc1de7243b00072f094045966df11c, reversing
    changes made to 463b994bd71658d0f9140008d3020893a656b2b8.
    [back_pulley_reinforcement_plate.SLDPRT, crossbar_pulley_reinforcement_plate.SLDPRT, left_alum_double_pulley_corner_bracket.STEP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]
2020-05-04 Revert "Revert "Merge remote-tracking branch 'upstream/master'""
    This reverts commit 79b8b6cca6ce005cb0a8f4527e5978af438a2a4d.
    [back_pulley_reinforcement_plate.SLDPRT, crossbar_pulley_reinforcement_plate.SLDPRT, left_alum_double_pulley_corner_bracket.STEP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]
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2020-05-19 adding 0.2mm z tolerance to printed pulley plates
    [back_pulley_reinforcement_plate.SLDPRT, crossbar_pulley_reinforcement_plate.SLDPRT, left_corner_pulley_reinforcement_plate.STL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]
2020-05-22 updating twist lock spacer OD and converting dangling ASCII STLs to binary
    [fixed_half_pulley.STL, floating_half_pulley.STL, lock_actuator_base_plate.STL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]
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2020-06-02 bugfixes in Z axis instructions
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2020-06-23 updating duet2 Zmotor wire color coding to match LDO wires
    [back_panel.DXF]
2020-06-24 swapping STL format to binary on groovemount clip
    [groovemount_clip.STL]
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2020-07-04 updating diameter of REL motor clip for LDO motor
    [lock_actuator_motor_clip.STL]
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2020-07-30 updating toolchange macros to better handle tools of mixed heights
    [tfree0.g, tfree1.g, tpost0.g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]
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2020-08-03 fixing Z plate wiring cable sleeving length
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2020-08-17 updating tc macros to be slightly more conservative; fixing config.g XY home location.
    [config.g, tfree0.g, tfree1.g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]
2020-08-17 restoring tc macro comment to remind user to update parking post positions to match their actual machine
    [tfree0.g, tfree1.g, tpre0.g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]
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2020-09-29 updating default extruder tool wings and duet2 configs
    [config.g, left_parking_wing.STL, ooze_wiper_assembly.STEP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]
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2020-10-08 fixing printed pulley spacer print orientation
    [printed_pulley_spacer.STL]
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2020-10-25 swapping m3 slide in T nut for stamped variant
2020-10-25 adding missing dimension in outer frame assembly instructions
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2020-11-06 swapping psu holder print orientation
    [psu_socket_holder.STL]
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2020-11-11 opening up front ZPlate holes to account for Slide-In TNut sizes
    [front_left_z_motor_plate.STL, front_right_z_motor_plate.STL]
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2020-11-29 Detect if there is a tool loaded before homing all (from ProbiusSC)
    [homeall.g, homeu.g]
2020-11-29 M400 is needed to ensure that the model has been updated
    [homeu.g]
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2020-11-29 Add curly brackets to make the abs evaluate
    [homeu.g]
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2020-12-01 Change homing order from YXUZ to UYXZ
    New tool detection has a pop up warning if Z or X is homed before U. U should be homed first so the popup doesn't appear.
    [homeall.g]
2020-12-01 Add tool detection capability
    Attempt to move the axis near it's maximum and stopping if it hits the endstop. If the endstop is triggered before the end of move move.axes[3].userPosition will read 0 instead of 170.
    [homeu.g]
2020-12-01 Update homey.g
    Increased max search distance to accommodate for homing from within the tool posts
    Removed unnecessary relief
    [homey.g]
2020-12-01 Update homeu.g
    Users reported not being able to reach 170deg. Potential miscalculation of steps/deg somewhere
    [homeu.g]
2020-12-01 Update homeu.g
    Corrected max travel value
    [homeu.g]
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2020-12-04 Added jammed endstop detection
    Throws error if relevant endstop was already triggered for XYZ homing. Detetction not added to U axis because both natual states leave it triggered.
    [homex.g, homey.g, homez.g]
2020-12-05 Can't home any axis in a home script, use macro calls
    [homex.g, homez.g]
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2021-01-31 swapping M3 10mm and 12mm screws in carriage and back z motor section
2021-02-03 flipping tool template
    [M3_countersunk_washer_OOTDTY.SLDPRT, base_tool_plate.SLDPRT, coupling_plate_insert.SLDPRT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]
2021-02-03 flipping wedge plate orientation on default bmg tool
    [bondtech_bmg_simplified.SLDPRT, bondtech_direct_drive_extruder_base_tool_plate.SLDPRT, bondtech_motor_gear.SLDPRT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]
2021-02-11 Replaced G28 with M98 P for RRF3.2 compatibility
    [homex.g, homez.g]
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2021-02-14 reverting resume.g on rrf3
    [resume.g]
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2021-03-14 adding tool wings as standalone STL, STEP, SLDPRT
    [left_tool_wing_v1.STEP, left_tool_wing_v1.STL, left_tool_wing_v2.STEP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]
2021-03-14 fixing rel motor spec in instructions
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2021-03-31 updating fan shroud to bring in edthesped's cappuccino fan shroud
    [blower_fan_shroud.STL, bondtech_bmg_simplified.SLDPRT, bondtech_motor_gear.SLDPRT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]
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2021-04-21 updating cappucino fan with 2mm extra slot width
    [COOLING-NOZZLE-edthesped.SLDPRT, Radial-Cooling-Fan-5015-DC12V.SLDPRT, blower_fan_shroud.STL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]
2021-05-30 duet2,rrf3 config bugfix on thermistor definition
    [config.g]
2021-05-30 config update. Moving Control Point to 2mm below limit switch trigger position.
    [config.g]
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2021-07-04 updating x axis hard stop width to 18.6mm
    [x_axis_hard_stop.STL]
2021-08-30 Update tool_lock.g
    adding overcurrent lines in tool_lock macro but commented out
    [tool_lock.g]
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2021-10-05 adding baby bullet threaded heatsink variant for v7 hotends
    [Radial-Cooling-Fan-5015-DC12V.SLDPRT, back_base_piece_assembly.SLDASM, base_tool_plate_assembly.SLDASM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]
2021-10-06 updating groovemount geometry and exporting threaded heatsink mount for baby bullet extruder
    [back_base_piece.STL, back_base_piece_assembly.SLDASM, base_tool_plate_assembly.SLDASM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]
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2021-10-06 adding M12 threaded heatsink wrench for baby bullet extruder assembly
    [carriage_back_plate.STL, carriage_center_plate.STL, lock_actuator_base_plate.STL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]
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2021-10-08 updating thr bb bullet to include tool plate screw clearance pocket
    [top_base_piece.STL]
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2021-10-16 updating STEP Files to be in sync with Solidworks files
    [back_base_piece_assembly.SLDASM, base_tool_plate_assembly.SLDASM, carriage_assembly.SLDASM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]
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2021-12-24 uploaded cads of tool dowel fixtures
    Tool to help press the tool dowel pins easier and more straight.
    When using this helping tool, you need to make sure it fully contacts the surface of the "parking_post_base"
    An arbor press is still recommended.
    [Tool_Dowel_Fixture-40mm.step, Tool_Dowel_Fixture-Parametric.f3d]
2021-12-24 uploaded Tool_Dowel_Fixtures stl files
    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
    [Tool_Dowel_Fixture_40mm.stl, Tool_Dowel_Fixture_43mm.stl, Tool_Dowel_Fixture_47mm.stl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]
2021-12-24 folder rename
    folder rename tool dowel fixture cads to tool_dowel_fixture_cads
    [Tool_Dowel_Fixture-40mm.step, Tool_Dowel_Fixture-Parametric.f3d]
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2022-02-07 fixed outer frame instructions erroneous text; updated sheet template
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2022-04-01 ading prelim duet3 mini config files; these should match the wiring diagram.;
    [bed.g, cancel.g, config.g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]
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2022-12-24 fix stl print orientation on bb bullet; update SW and STEP files on bb bullet
    [4mm Bowden Coupler v1_1.SLDASM, 4mm Bowden Coupler v1_1.SLDPRT, 4mm Bowden Coupler v1_1_2.SLDPRT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]
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2023-01-05 fix ZL ZR ZB mixup in duet3 mini wiring pdf
